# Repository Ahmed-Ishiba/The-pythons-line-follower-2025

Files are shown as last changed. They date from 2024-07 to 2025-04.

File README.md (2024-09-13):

# Robocup-The Pythons

This is a documentation of our journey in the Robocup competition in line-follower category, the team members are Ahmed Ibrahim Elsayed (me), Moaz Ahmed, Eyad Ahmed, Nour Eldin Raoof each are responsible for the programming , electrical and Mechanical part of the robot respectively and our coach Omar Ahmed Khaled.

This documentation will list the components used , the thought process that went into making this robot and the algorithm of our line-following and evacuation zone

## Compontents used:
| Name | Price | Weight | Link|
|---|---|---|-----|
|Pololu wheels|9.95 USD|23gm|https://www.pololu.com/product/3691|
|Omni wheels|35 USD| 49gm|https://www.robotshop.com/products/70mm-omni-wheel-4mm-bore |
|133rpm Motors| 360 EGP|88gm|https://makerselectronics.com/product/dc-motor-with-gear-box-jga25-370-12v-133rpm-20kg-cm |
|Raspberry pi5 8gb ram| 80USD|76gm|https://www.adafruit.com/product/5813|
|Raspberry pi camera module3|35 USD|5gm|https://www.adafruit.com/product/5658|
|Adafruit DRV8871 motor driver|7.5 USD|5gm|https://www.adafruit.com/product/3190|
|Adafruit Time of Flight sensor|14.95 USD|2gm|https://www.adafruit.com/product/3317|
|10 DOF IMU|920 EGP|2gm|https://store.fut-electronics.com/products/10-dof-imu-mpu9250-bmp280?_pos=3&_sid=8a9a77714&_ss=r |
|InfraRed obstacle sensor|75 EGP|3gm|https://store.fut-electronics.com/products/infrared-obstacle-avoidance-sensor-ky-032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|
|Microservo MG90S|140 EGP|17gm|https://makerselectronics.com/product/micro-servo-mg90s-full-metal-gear-180-degree|
|Hiwonder full metal gear|18.99 USD |101gm|https://www.hiwonder.com/products/hps-2018?_pos=16&_sid=3165c6d7c&_ss=r|
|XL 4015 step down dc convertor|115 EGP| 21 gm|https://makerselectronics.com/product/xl4015-step-down-dc-module-with-cv-cc-control|
|LM-2596S DC-DC convertor| 55 EGP |13gm|https://makerselectronics.com/product/lm2596s-dc-dc-converter-3a-step-down-module|
|XL-4016 Step down convertos| 260 EGP|75 gm | https://ampere-electronics.com/product/xl4016-dc-dc-step-down-converter-module-12a-300w/|
|Cytron dual channel motor driver| 1750 EGP | 33gm| https://store.fut-electronics.com/products/dual-channel-dc-motor-driver-10a-each|

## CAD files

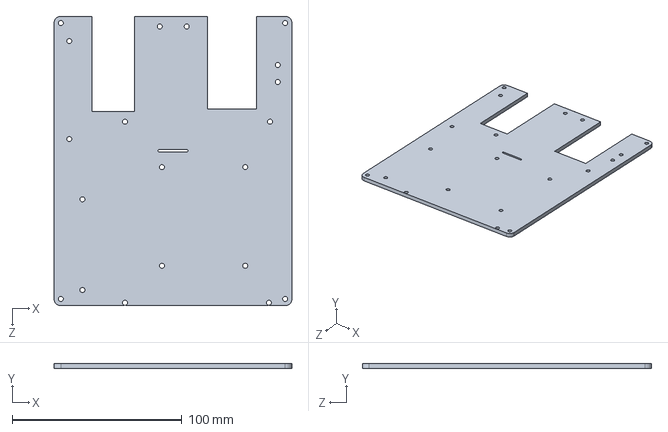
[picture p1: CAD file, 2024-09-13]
mechanical/Floor 2 2nd.SLDPRT
140.0 x 3.00 x 170.3 mm

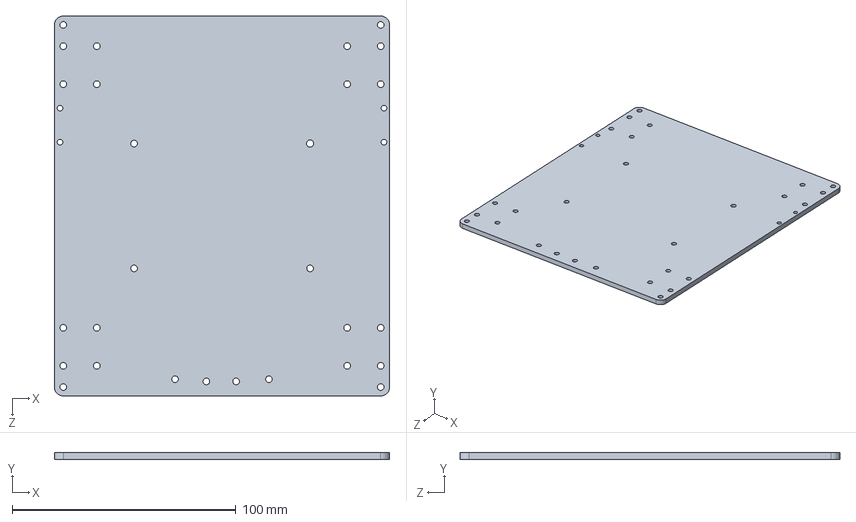
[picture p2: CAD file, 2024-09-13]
mechanical/Floor 1 2nd .SLDPRT
150.0 x 3.00 x 170.0 mm

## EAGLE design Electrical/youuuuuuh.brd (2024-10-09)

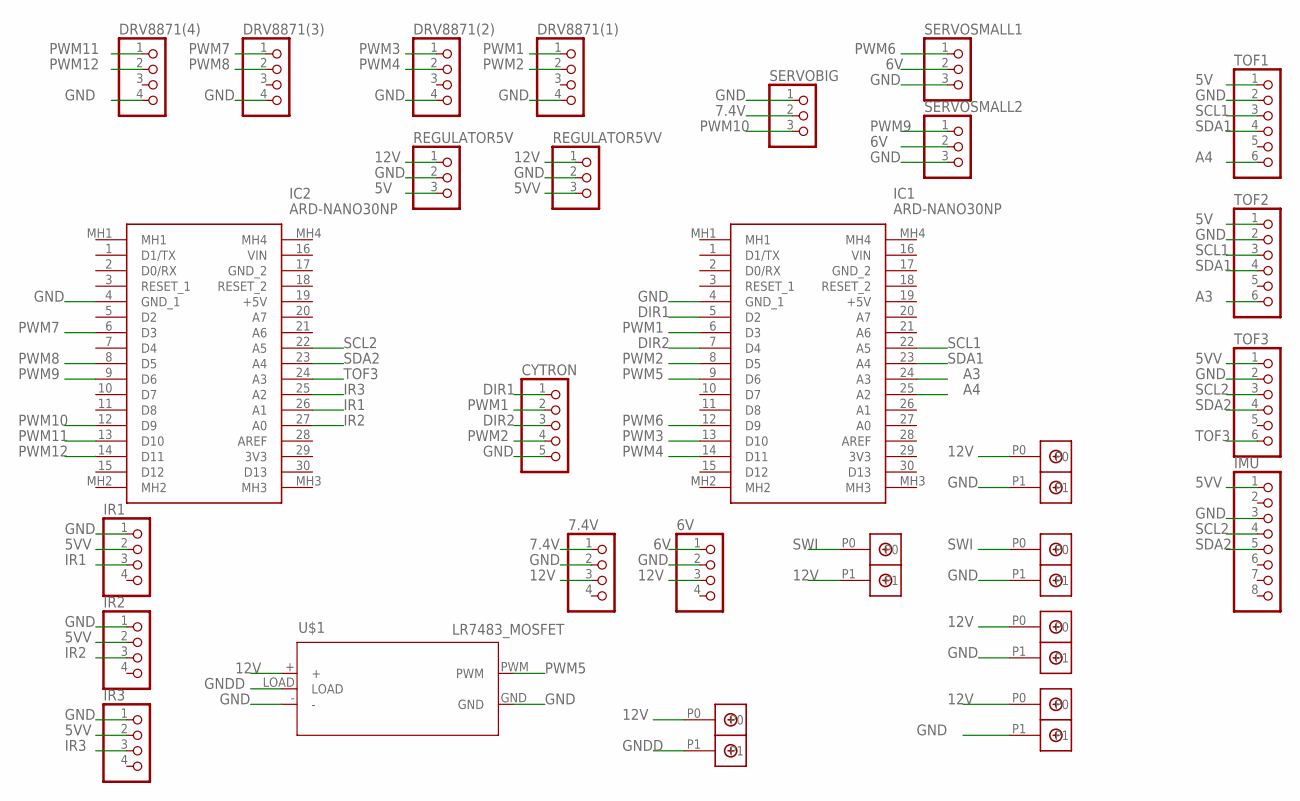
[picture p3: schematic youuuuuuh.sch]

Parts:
6V, 7.4V: PINHD-1X4; 1X04
BATERY: DBCONN-1X2
BUCKSERVO: DBCONN-1X2
CYTRON: PINHD-1X5; 1X05
CYTRONPOWER: DBCONN-1X2
DRV8871(1), DRV8871(2), DRV8871(3), DRV8871(4): PINHD-1X4; 1X04
IC1, IC2: ARD-NANO30NP; ARDNANO30NP
IMU: PINHD-1X8; 1X08
IR1, IR2, IR3: PINHD-1X4; 1X04
LEDS1, LEDS2, LEDS3: DBCONN-1X2
REGULATOR5V, REGULATOR5VV: PINHD-1X3; 1X03
SERVOBIG: PINHD-1X3; 1X03
SERVOSMALL1, SERVOSMALL2: PINHD-1X3; 1X03
TOF1, TOF2, TOF3: PINHD-1X6; 1X06
U$1: LR7483_MOSFET

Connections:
5V: REGULATOR5V.3, TOF1.1, TOF2.1
5VV: IMU.1, IR1.2, IR2.2, IR3.2, REGULATOR5VV.3, TOF3.1
6V: 6V.1, SERVOSMALL1.2, SERVOSMALL2.2
7.4V: 7.4V.1, SERVOBIG.2
12V: 6V.3, 7.4V.3, BUCKSERVO.P0, CYTRONPOWER.P0, LEDS1.P1, LEDS2.P0, LEDS3.P0, REGULATOR5V.1, REGULATOR5VV.1, U$1.+
A3: IC1.24 (A3), TOF2.6
A4: IC1.25 (A2), TOF1.6
DIR1: CYTRON.1, IC1.5 (D2)
DIR2: CYTRON.3, IC1.7 (D4)
GND: 6V.2, 7.4V.2, BATERY.P1, BUCKSERVO.P1, CYTRON.5, CYTRONPOWER.P1, DRV8871(1).4, DRV8871(2).4, DRV8871(3).4, DRV8871(4).4, IC1.4 (GND_1), IC2.4 (GND_1), IMU.3, IR1.1, IR2.1, IR3.1, LEDS2.P1, REGULATOR5V.2, REGULATOR5VV.2, SERVOBIG.1, SERVOSMALL1.3, SERVOSMALL2.3, TOF1.2, TOF2.2, TOF3.2, U$1.-, U$1.GND
GNDD: LEDS3.P1, U$1.LOAD
IR1: IC2.26 (A1), IR1.3
IR2: IC2.27 (A0), IR2.3
IR3: IC2.25 (A2), IR3.3
PWM1: CYTRON.2, DRV8871(1).1, IC1.6 (D3)
PWM2: CYTRON.4, DRV8871(1).2, IC1.8 (D5)
PWM3: DRV8871(2).1, IC1.13 (D10)
PWM4: DRV8871(2).2, IC1.14 (D11)
PWM5: IC1.9 (D6), U$1.PWM
PWM6: IC1.12 (D9), SERVOSMALL1.1
PWM7: DRV8871(3).1, IC2.6 (D3)
PWM8: DRV8871(3).2, IC2.8 (D5)
PWM9: IC2.9 (D6), SERVOSMALL2.1
PWM10: IC2.12 (D9), SERVOBIG.3
PWM11: DRV8871(4).1, IC2.13 (D10)
PWM12: DRV8871(4).2, IC2.14 (D11)
SCL1: IC1.22 (A5), TOF1.3, TOF2.3
SCL2: IC2.22 (A5), IMU.4, TOF3.3
SDA1: IC1.23 (A4), TOF1.4, TOF2.4
SDA2: IC2.23 (A4), IMU.5, TOF3.4
SWI: BATERY.P0, LEDS1.P0
TOF3: IC2.24 (A3), TOF3.6

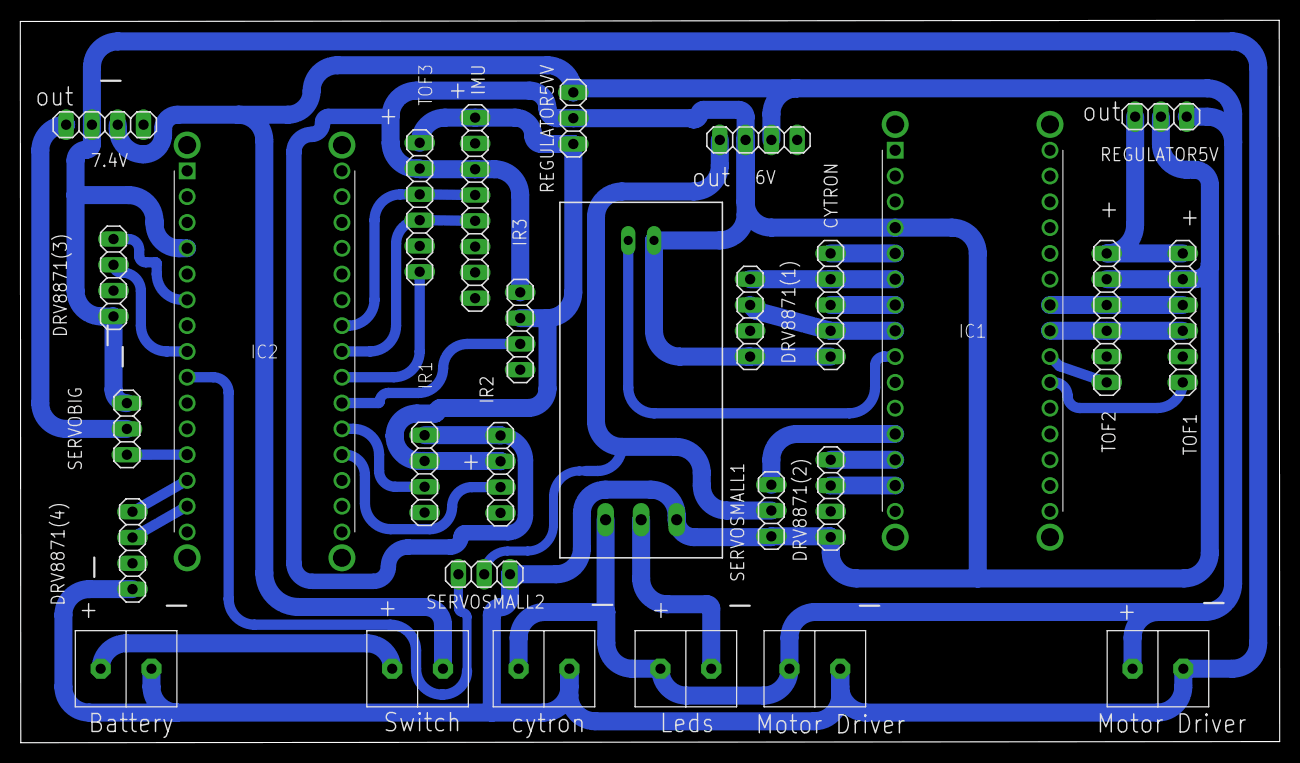
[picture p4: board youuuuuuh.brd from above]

Board: 2 copper layers, 124.0 x 71.1 mm, 28 parts (0 on the bottom side), 32 nets.

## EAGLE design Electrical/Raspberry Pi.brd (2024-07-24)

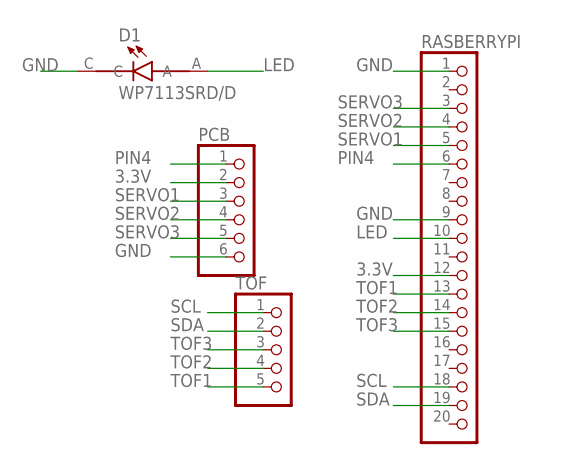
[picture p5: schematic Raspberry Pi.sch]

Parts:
D1: WP7113SRD/D; LED_WP7113SRD/D
PCB: PINHD-1X6; 1X06
RASBERRYPI: PINHD-1X20; 1X20
TOF: PINHD-1X5; 1X05

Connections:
3.3V: PCB.2, RASBERRYPI.12
GND: D1.C, PCB.6, RASBERRYPI.1, RASBERRYPI.9
LED: D1.A, RASBERRYPI.10
PIN4: PCB.1, RASBERRYPI.6
SCL: RASBERRYPI.18, TOF.1
SDA: RASBERRYPI.19, TOF.2
SERVO1: PCB.3, RASBERRYPI.5
SERVO2: PCB.4, RASBERRYPI.4
SERVO3: PCB.5, RASBERRYPI.3
TOF1: RASBERRYPI.13, TOF.5
TOF2: RASBERRYPI.14, TOF.4
TOF3: RASBERRYPI.15, TOF.3

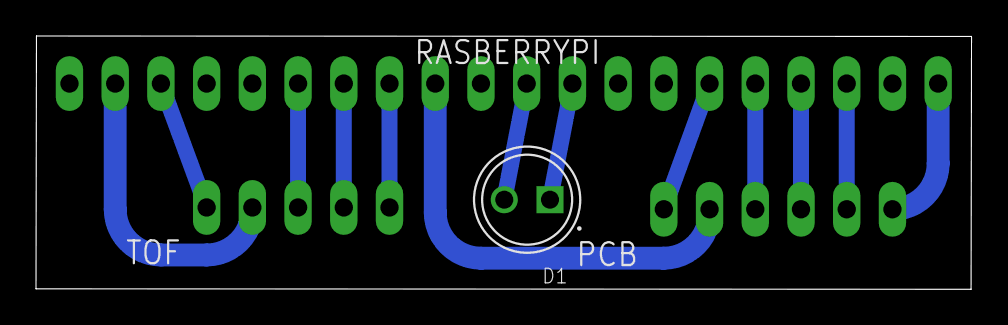
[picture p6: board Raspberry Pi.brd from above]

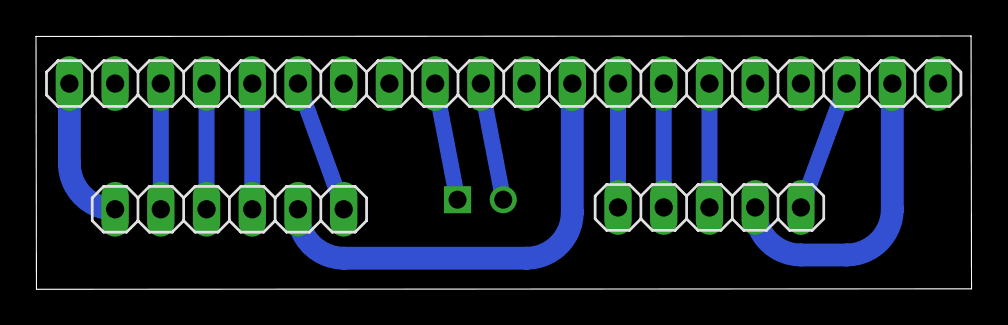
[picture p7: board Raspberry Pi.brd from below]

Board: 2 copper layers, 52.0 x 14.1 mm, 4 parts (3 on the bottom side), 12 nets.

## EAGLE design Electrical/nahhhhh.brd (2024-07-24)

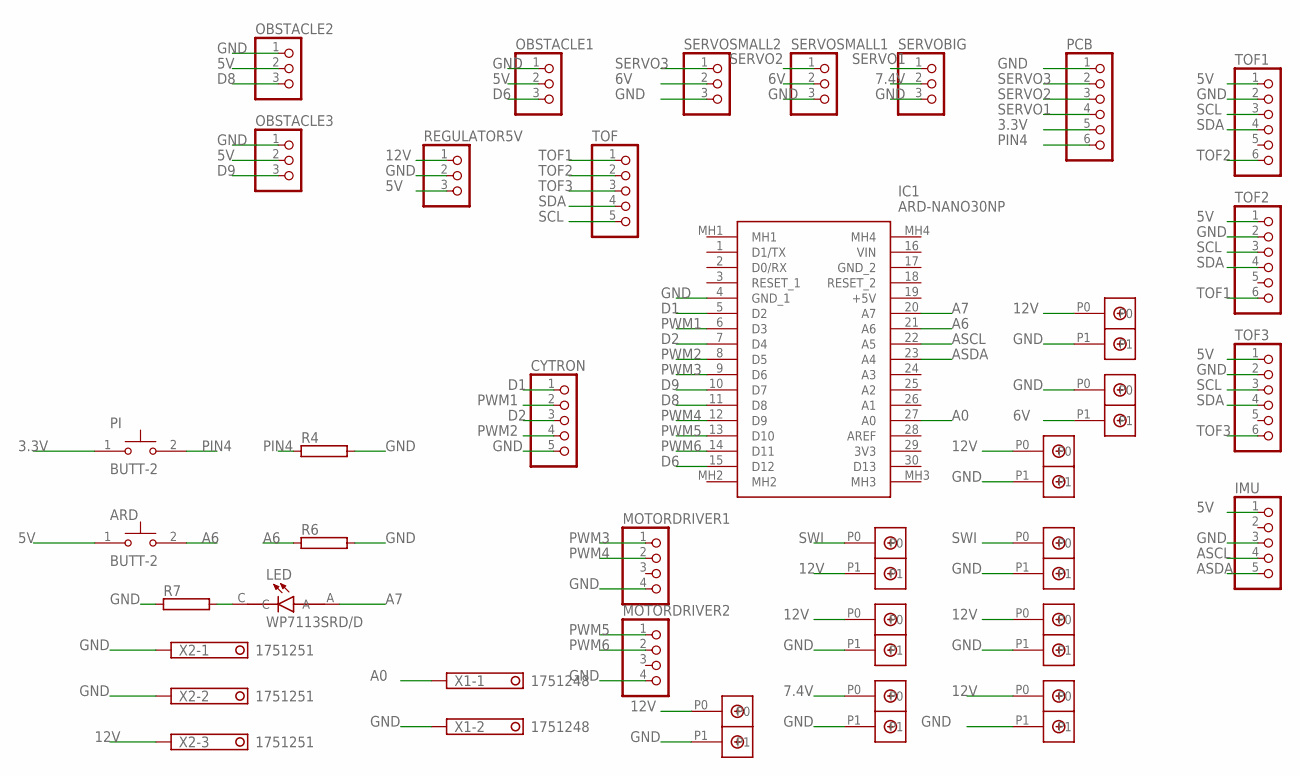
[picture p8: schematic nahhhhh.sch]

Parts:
ARD: BUTT-2; SW_BUTT-2
BATERY: DBCONN-1X2
BUCKSERVO: DBCONN-1X2
CYTRON: PINHD-1X5; 1X05
CYTRONPOWER: DBCONN-1X2
IC1: ARD-NANO30NP; ARDNANO30NP
IMU: PINHD-1X5; 1X05
LED: WP7113SRD/D; LED_WP7113SRD/D
LEDS, LEDS1, LEDS2, LEDS3, LEDS4, LEDS5: DBCONN-1X2
MOTORDRIVER1, MOTORDRIVER2: PINHD-1X4; 1X04
OBSTACLE1, OBSTACLE2, OBSTACLE3: PINHD-1X3; 1X03
PCB: PINHD-1X6; 1X06
PI: BUTT-2; SW_BUTT-2
R4, R6, R7: RHPS58; HPS58
REGULATOR5V: PINHD-1X3; 1X03
SERVOBIG: PINHD-1X3; 1X03
SERVOSMALL1, SERVOSMALL2: PINHD-1X3; 1X03
TOF: PINHD-1X5; 1X05
TOF1, TOF2, TOF3: PINHD-1X6; 1X06
U$1: DBCONN-1X2
X1: 1751248
X2: 1751251

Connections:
3.3V: PCB.5, PI.1
5V: ARD.1, IMU.1, OBSTACLE1.2, OBSTACLE2.2, OBSTACLE3.2, REGULATOR5V.3, TOF1.1, TOF2.1, TOF3.1
6V: LEDS5.P1, SERVOSMALL1.2, SERVOSMALL2.2
7.4V: SERVOBIG.2, U$1.P0
12V: BUCKSERVO.P0, CYTRONPOWER.P0, LEDS.P0, LEDS1.P1, LEDS2.P0, LEDS3.P0, LEDS4.P0, REGULATOR5V.1, X2.3
A0: IC1.27 (A0), X1.1
A6: ARD.2, IC1.21 (A6), R6.1
A7: IC1.20 (A7), LED.A
ASCL: IC1.22 (A5), IMU.4
ASDA: IC1.23 (A4), IMU.5
D1: CYTRON.1, IC1.5 (D2)
D2: CYTRON.3, IC1.7 (D4)
D6: IC1.15 (D12), OBSTACLE1.3
D8: IC1.11 (D8), OBSTACLE2.3
D9: IC1.10 (D7), OBSTACLE3.3
GND: BATERY.P1, BUCKSERVO.P1, CYTRON.5, CYTRONPOWER.P1, IC1.4 (GND_1), IMU.3, LEDS.P1, LEDS2.P1, LEDS3.P1, LEDS4.P1, LEDS5.P0, MOTORDRIVER1.4, MOTORDRIVER2.4, OBSTACLE1.1, OBSTACLE2.1, OBSTACLE3.1, PCB.1, R4.2, R6.2, R7.1, REGULATOR5V.2, SERVOBIG.3, SERVOSMALL1.3, SERVOSMALL2.3, TOF1.2, TOF2.2, TOF3.2, U$1.P1, X1.2, X2.1, X2.2
unnamed: LED.C, R7.2
PIN4: PCB.6, PI.2, R4.1
PWM1: CYTRON.2, IC1.6 (D3)
PWM2: CYTRON.4, IC1.8 (D5)
PWM3: IC1.9 (D6), MOTORDRIVER1.1
PWM4: IC1.12 (D9), MOTORDRIVER1.2
PWM5: IC1.13 (D10), MOTORDRIVER2.1
PWM6: IC1.14 (D11), MOTORDRIVER2.2
SCL: TOF.5, TOF1.3, TOF2.3, TOF3.3
SDA: TOF.4, TOF1.4, TOF2.4, TOF3.4
SERVO1: PCB.4, SERVOBIG.1
SERVO2: PCB.3, SERVOSMALL1.1
SERVO3: PCB.2, SERVOSMALL2.1
SWI: BATERY.P0, LEDS1.P0
TOF1: TOF.1, TOF2.6
TOF2: TOF.2, TOF1.6
TOF3: TOF.3, TOF3.6

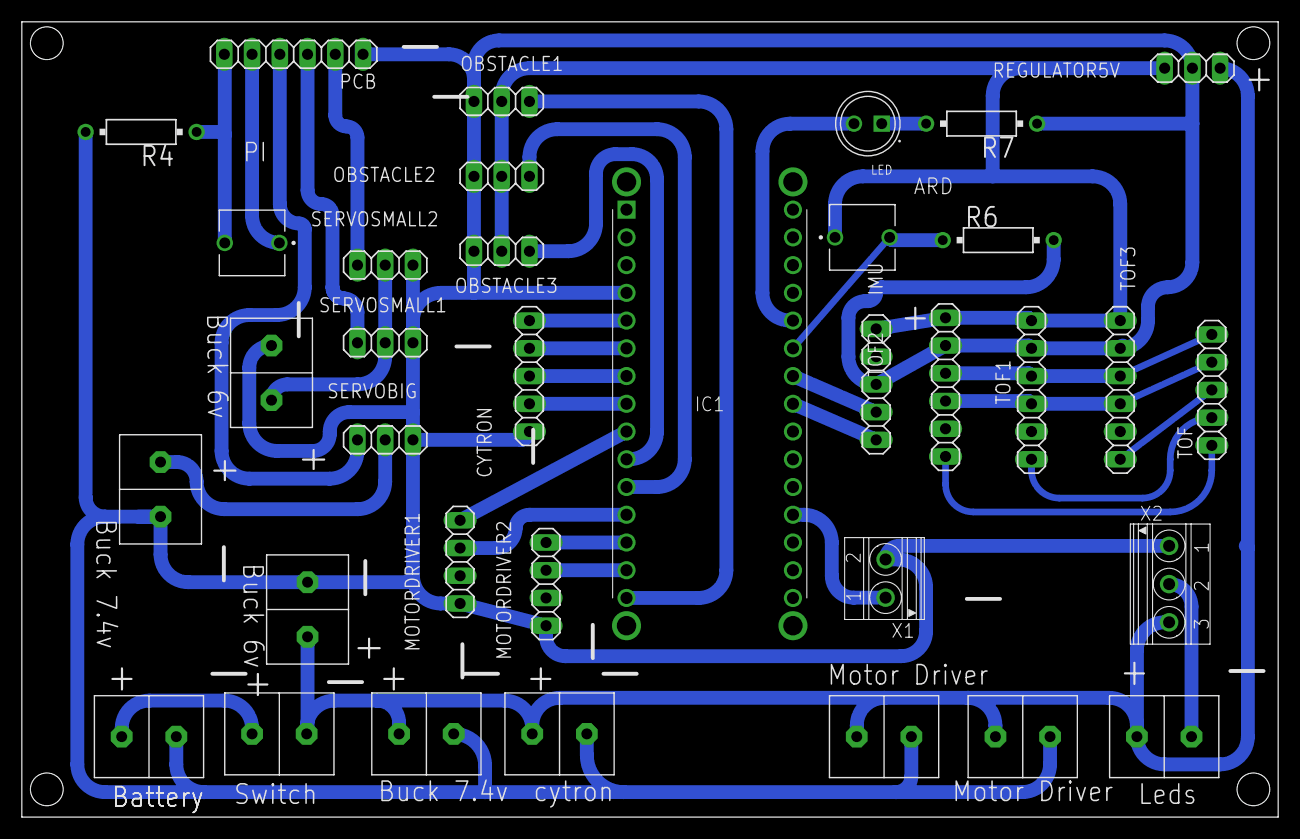
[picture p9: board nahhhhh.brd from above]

Board: 2 copper layers, 115.0 x 72.8 mm, 35 parts (0 on the bottom side), 33 nets.

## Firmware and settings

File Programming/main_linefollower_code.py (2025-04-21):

from __future__ import division

script = True
turn_off_motion = False
turn_off_drawing = True
detect_red = False

import time
from ultralytics import YOLO
import board
import gpiod
import busio
from adafruit_mpu6050 import MPU6050
import Adafruit_PCA9685
import Adafruit_GPIO.I2C as I2C
from adafruit_motor import servo
from adafruit_pca9685 import PCA9685
import os
import sys
import smbus
import cv2
from picamera2 import Picamera2
import numpy as np
import math
from time import sleep
from operator import itemgetter
weights = [0.3,0.6,0.7] 
arr_higher_threshold = [np.array([149,188,176], np.uint8),np.array([149,188,176], np.uint8),np.array([149,188,176], np.uint8)]
arr_lower_threshold = [np.array([115,114,12], np.uint8), np.array([115,114,12], np.uint8), np.array([115,114,12], np.uint8)]

picam2 = Picamera2(0)
picam2.preview_configuration.main.size=(320,240) #full screen : 3280 2464
picam2.preview_configuration.main.format = "RGB888" #8 bits
picam2.start()
centroid_sum = 0
center_pos = 0


i2c = board.I2C()
i2c_bus = 1
pwm = Adafruit_PCA9685.PCA9685(address=0x40, busnum=i2c_bus)
try:
	OFFSET_X = 0
	OFFSET_Y = 0
	OFFSET_Z = 0

	mpu = MPU6050(i2c)
	mpu.accelerometer_offset = (OFFSET_X, OFFSET_Y, OFFSET_Z)
except:
	pass



f = gpiod.LINE_REQ_FLAG_BIAS_PULL_DOWN
chip = gpiod.Chip('gpiochip4')
led = chip.get_line(20)#20
led.request("p_gpio", gpiod.LINE_REQ_DIR_OUT, f)
led.set_value(1)
time.sleep(1)
led.set_value(0)


pca = PCA9685(i2c)
pca.frequency = 50

check_zone = False

pwm.set_pwm_freq(60)

left_front_1 = 14
left_front_2 = 15

left_back_1 = 9
left_back_2 = 8

right_front_1 = 12
right_front_2 = 13

right_back_1 = 10
right_back_2 = 11

high_speed = 900
speed2 =0
low_speed  = 700
zero_speed = 0
counter =0
model = YOLO("/home/pi/yolo/silver_classify_s.onnx", task='classify')
def entrance(im):
    global check_zone
    global counter, enter_zone
    #picam1.set_controls({"AeEnable":False, "ExposureTime":4000}) #To be tested
    results = model.predict(im, imgsz=128, conf=0.2, workers=4,verbose=False)
    result=results[0].numpy()
    confidences = result.probs.top5conf
    silver_value = confidences[0] if result.probs.top1 == 1 else confidences[1]
    print("confidance",silver_value)
    if silver_value >0.2:
        print("saw silver")
        counter+=1
    else:
        counter =0
    if counter > 0:
        enter_zone = True
        print("evacuation")
        """
        with open("/tmp/switch_script","w") as f:
            f.write("switch")
        time.sleep(2)
        """
        
     
    
def calculate_orientation():
    accel_x, accel_y, accel_z = mpu.acceleration
    # Calculate pitch and roll angles
    pitch = math.atan2(accel_x, math.sqrt(accel_y**2 + accel_z**2)) * 180 / math.pi
    roll = math.atan2(-accel_y, accel_z) * 180 / math.pi

    # Convert to range -180 to 180
    if pitch > 180:
        pitch -= 360
    if roll > 180:
        roll -= 360

    return pitch, roll

def map_value(value, from_low, from_high, to_low, to_high):
    if from_high - from_low == 0:
        return to_low  
    mapped_value = (value - from_low) / (from_high - from_low) * (to_high - to_low) + to_low
    return mapped_value

def turn_around():
    backward()
    time.sleep(0.5)
    right(1000)
    time.sleep(1.5)

def forward():
    global speed2
    pwm.set_pwm(left_front_1, 0, 500+speed2)
    pwm.set_pwm(left_front_2, 0, 0)
	
    pwm.set_pwm(left_back_1, 0, 500+speed2)
    pwm.set_pwm(left_back_2, 0, 0)
	
    pwm.set_pwm(right_front_1, 0, 500+speed2)
    pwm.set_pwm(right_front_2, 0, 0)
	
    pwm.set_pwm(right_back_1, 0, 500+speed2)
    pwm.set_pwm(right_back_2, 0, 0)
def backward():
    pwm.set_pwm(left_front_2, 0, 600)
    pwm.set_pwm(left_front_1, 0, 0)
	
    pwm.set_pwm(left_back_2, 0, 600)
    pwm.set_pwm(left_back_1, 0, 0)
	
    pwm.set_pwm(right_front_2, 0, 600)
    pwm.set_pwm(right_front_1, 0, 0)
	
    pwm.set_pwm(right_back_2, 0, 600)
    pwm.set_pwm(right_back_1, 0, 0)
def right(speed):
    pwm.set_pwm(left_front_1, 0, speed)
    pwm.set_pwm(left_front_2, 0, 0)
	
    pwm.set_pwm(left_back_1, 0, 400)
    pwm.set_pwm(left_back_2, 0, 0)
    
    pwm.set_pwm(right_front_2, 0, speed)
    pwm.set_pwm(right_front_1, 0, 0)
	
    pwm.set_pwm(right_back_2, 0, 400)
    pwm.set_pwm(right_back_1, 0, 0)
def left(speed):
    pwm.set_pwm(left_front_2, 0, speed)
    pwm.set_pwm(left_front_1, 0, 0)
	
    pwm.set_pwm(left_back_2, 0, 400)
    pwm.set_pwm(left_back_1, 0, 0)
	
    pwm.set_pwm(right_front_1, 0, speed)
    pwm.set_pwm(right_front_2, 0, 0)
	
    pwm.set_pwm(right_back_1, 0, 400)
    pwm.set_pwm(right_back_2, 0, 0)
def stop():
    pwm.set_pwm(left_front_2, 0, 900)
    pwm.set_pwm(left_front_1, 0, 0)
    pwm.set_pwm(left_back_2, 0, 900)
    pwm.set_pwm(left_back_1, 0, 0)
    pwm.set_pwm(right_front_2, 0, 900)
    pwm.set_pwm(right_front_1, 0, 0)
    pwm.set_pwm(right_back_2, 0, 900)
    pwm.set_pwm(right_back_1, 0, 0)
    time.sleep(0.1)
    pwm.set_pwm(left_front_1, 0, 0)
    pwm.set_pwm(left_front_2, 0, 0)
    pwm.set_pwm(left_back_1, 0, 0)
    pwm.set_pwm(left_back_2, 0, 0)
    pwm.set_pwm(right_front_1, 0, 0)
    pwm.set_pwm(right_front_2, 0, 0)
    pwm.set_pwm(right_back_1, 0, 0)
    pwm.set_pwm(right_back_2, 0, 0)

def obstacle_left():
	left(1000)
	time.sleep(0.6)
	stop()
	time.sleep(0.2)
	forward()
	time.sleep(0.9)
	stop()
	time.sleep(0.2)
	right(1000)
	time.sleep(0.7)
	stop()
	time.sleep(0.2)
	forward()
	time.sleep(1.3)
	stop()
	time.sleep(0.2)
	right(1000)
	time.sleep(0.7)
	stop()
	time.sleep(0.2)
	forward()
	time.sleep(0.7)
	stop()
	time.sleep(0.2)
	left(1000)
	time.sleep(0.7)
	stop()
	time.sleep(5)
	
def obstacle_right():
	right(1000)
	time.sleep(0.6)
	stop()
	time.sleep(0.2)
	forward()
	time.sleep(0.9)
	stop()
	time.sleep(0.2)
	left(1000)
	time.sleep(0.7)
	stop()
	time.sleep(0.2)
	forward()
	time.sleep(1.3)
	stop()
	time.sleep(0.2)
	left(1000)
	time.sleep(0.7)
	stop()
	time.sleep(0.2)
	forward()
	time.sleep(0.7)
	stop()
	time.sleep(0.2)
	right(1000)
	time.sleep(0.7)
	stop()
	time.sleep(5)

"""
hoigher =  (179, 106, 101)
lower =  (91, 27, 12)


"""
black_lower = np.array([91, 27, 12], np.uint8)
black_upper =np.array([179, 106, 101], np.uint8)
def detect_triangles(im):
    cropped_image = im[140:200, 15:305] #140:230,:320
    cx, cy, w, h =0,0,0,0
    triangle_area = 0
    right_zigzag, left_zigzag = False, False
    theta = 0
    global black_lower
    global black_upper
    hsvf = cv2.cvtColor(cropped_image, cv2.COLOR_BGR2HSV)
    black_mask = cv2.inRange(hsvf, black_lower, black_upper)
    black_result = cv2.bitwise_and(cropped_image, cropped_image, mask=black_mask)
    black_contours, black_hierarchy = cv2.findContours(black_mask, cv2.RETR_TREE, cv2.CHAIN_APPROX_SIMPLE)
    if len(black_contours)>0:
        largest_black = max(black_contours, key=cv2.contourArea)
        if not(turn_off_drawing):
            cv2.drawContours(cropped_image,largest_black,-1,(255, 0, 0), 3)
        approx = cv2.approxPolyDP(largest_black, 0.021*cv2.arcLength(largest_black, True), True)#0.025, 0.23
        x, y, w, h = cv2.boundingRect(largest_black)
        print("len approx", len(approx))
        if len(approx) ==3:
            triangle_area = cv2.contourArea(largest_black)
            print("triangle area = ", triangle_area)
            print("approx", approx[0][0][0])
            p1 = (approx[0][0][0], approx[0][0][1])
            p2 = (approx[1][0][0], approx[1][0][1])
            p3 = (approx[2][0][0], approx[2][0][1])
            point_array = [p1, p2, p3]
            point_array = sorted(point_array, key = itemgetter(1))
            print(point_array)
            a = point_array[0]
            b = point_array[1] #down left point
            c = point_array[2] #down right point
            
            distance_ab = math.dist(a, b)
            distance_ac = math.dist(a, c)
            
            vector_AB = (b[0]-a[0], b[1]-a[1])
            vector_AC = (c[0]-a[0], c[1]-a[1])
            dot_AB_AC = vector_AB[0]*vector_AC[0] + vector_AB[1]*vector_AC[1]
            theta = math.acos((dot_AB_AC)/(distance_ab*distance_ac))
            cv2.circle(cropped_image, a, 5, (255, 255, 255), 3)
            cv2.circle(cropped_image, b, 5, (0, 0, 255), 3)
            cv2.circle(cropped_image, c, 5, (255, 0, 0), 3)
            
            if theta <5 and triangle_area > 50 :
                
                if distance_ab > distance_ac:    # >
                    triangle_x = b[0]
                    print("left zigzag test")
                    left_zigzag = True
                    '''
                    if triangle_x >160:
                        #print("right zigzag")
                        right_zigzag = True
                    elif triangle_x < 160:
                        #print("left zigzag")
                        left_zigzag = True
                    '''
                elif distance_ac> distance_ab: #>
                    triangle_x = c[0]
                    print("right zigzag test")
                    right_zigzag = True
                    '''
                    if triangle_x >160:
                        right_zigzag = True
                        #print("right zigzag")
                    elif triangle_x < 160:
                        left_zigzag = True
                        #print("left zigzag")
                    '''
                print("distance of AB", distance_ab)
                print("distance of AC", distance_ac)
                #if not(turn_off_drawing):
                cv2.drawContours(cropped_image,largest_black,0,(255, 255, 0), 3)
    
            else:
                left_zigzag = False
                right_zigzag = False
        else:
            left_zigzag = False
            right_zigzag = False
        #cx = int(x) + int(w/2)
        #cy = int(y) + int(h/2)
    return right_zigzag, left_zigzag, theta, triangle_area

"""
hoigher =  (175, 80, 92)
lower =  (3, 0, 29)
""" 
right_array = []
left_array = []
is_black =0
omar_right_counter =0 
omar_left_counter =0
readings_range=75
def omar_function(live):
    cropped_image = [live[140:200, 15:55],live[140:200,265:305]] 
    cx, y, w, h =0,0,0,0
    global right_array
    global omar_right_counter
    global omar_left_counter 
    global left_array 
    global is_black
    global black_lower
    global black_upper
    for i,region in enumerate(cropped_image):
        
        hsvf = cv2.cvtColor(region, cv2.COLOR_BGR2HSV)
        black_mask = cv2.inRange(hsvf, black_lower, black_upper)
        black_result = cv2.bitwise_and(region, region, mask=black_mask)
        black_contours, black_hierarchy = cv2.findContours(black_mask, cv2.RETR_TREE, cv2.CHAIN_APPROX_SIMPLE)
        is_black =0
        if black_contours:
            largest_black = max(black_contours, key=cv2.contourArea)
            area = cv2.contourArea(largest_black)
            x, y, w, h = cv2.boundingRect(largest_black)
            
            if area >150:
                cv2.rectangle(region,(x,y),(x+w,y+h), (255,0,0), 2)
                is_black = 1
        if i == 1:
            if len(right_array)==readings_range:
                omar_right_counter += -1 if right_array[0] else 1
                del right_array[0]
            right_array.append(is_black)
            omar_right_counter +=1 if is_black else -1
        elif i == 0:
            if len(left_array)==readings_range:
                omar_left_counter += -1 if left_array[0] else 1
                del left_array[0]
            left_array.append(is_black)
            omar_left_counter += 1 if is_black else -1
            
    omar_left_counter = readings_range if omar_left_counter >readings_range else omar_left_counter
    omar_left_counter = -readings_range if omar_left_counter <-readings_range else omar_left_counter
    
    omar_right_counter = readings_range if omar_right_counter >readings_range else omar_right_counter
    omar_right_counter = -readings_range if omar_right_counter <-readings_range else omar_right_counter
        
    

def black(live):
    #cropped_image = [live[70:110,15:305],live[120:160,15:305],live[170:240, 15:305]] #y, x
    #cropped_image = [live[90:130,15:305],live[140:180,15:305],live[190:240, 15:305]] #y, x
    cropped_image = [live[80:110,15:305],live[120:160,15:305],live[170:200, 15:305]] #y, x
    global detect_black #cropped_image = [live[90:130,15:305],live[140:180,15:305],live[190:240, 15:305]] y, x
    #cropped_image = [live[80:120,15:305],live[130:170,15:305],live[180:230, 15:305]] #y, x 2adema sh8al kelaby
    centroid_sum = 0 
    cy = 0
    cx_array =[]
    cy_correction_array = [80, 120, 170]
    cy_array = []
    area_array = []
    black_contour_list = []
    deflection_angle = 0
    w = 0
    center_pos = 0
    main_x =0
    cx = 0
    h = 0
    last_width = 0
    last_area = 0
    info_tuple = []
    area = 0
    gap_counter =0
    weight_sum=0
    
    for i,region in enumerate(cropped_image):
        cx_diff = 160
        last_cy = 0
        global black_lower
        global black_upper
        hsvf = cv2.cvtColor(region, cv2.COLOR_BGR2HSV)
        black_mask = cv2.inRange(hsvf, black_lower, black_upper)
        black_result = cv2.bitwise_and(region, region, mask=black_mask)
        black_contours, black_hierarchy = cv2.findContours(black_mask, cv2.RETR_TREE, cv2.CHAIN_APPROX_SIMPLE)
        if len(black_contours) > 0:
            largest_black = max(black_contours, key=cv2.contourArea)
            selected_black=largest_black
            area = cv2.contourArea(selected_black)
            if(area > 800):
       
                print("area",area)
                #cv2.drawContours(region, largest_black, -1, (255, 0, 0), 3)
                #print("x of black line", x)
                print("height of black",h)
                #return cx, cy
                black_contours = sorted(black_contours, key = cv2.contourArea, reverse=True)
                for blacks in black_contours:
                    area = cv2.contourArea(blacks)
                    if area < 800:
                        break
                    M = cv2.moments(blacks)
                    if M["m00"] != 0:
                        cx =int(M["m10"]/M["m00"])
                        cy =int(M["m01"]/M["m00"]) + cy_correction_array[i]
                        
                    if i ==2:
                        print("cx ", cx)
                        print("cy ", cy)
                        
                        print("last cy ", last_cy)
                        print("cx diffrence ", cx_diff)
                        
                        if cy > last_cy and abs(cx-160) <cx_diff:
                            selected_black = blacks
                            last_cy = cy
                            
                            cx_diff=abs(cx-160)
                            print("last cy", last_cy)
                        x, y, w, h = cv2.boundingRect(selected_black)
                        main_x = x
                        last_width = w
                    else:
                        if abs(cx-160) <cx_diff:
                            selected_black = blacks
                            cx_diff=abs(cx-160)
                area = cv2.contourArea(selected_black)
                M = cv2.moments(selected_black)
                if M["m00"] != 0:
                    cx =int(M["m10"]/M["m00"])
                    cy =int(M["m01"]/M["m00"]) + cy_correction_array[i]
                    
                    if len(cx_array) and i==1 and abs(cx-cx_array[0])>100:
                        cx_array[0]=0
                    cx_array.append(cx)
                    info_tuple.append((cx,cy, area))
                    cv2.circle(region, (cx, cy- cy_correction_array[i]), 2, (255, 0, 0), 1)
                x, y, w, h = cv2.boundingRect(selected_black)
                #cv2.rectangle(region,(x,y),(x+w,y+h), (220,220,220), 2)
            else:
                cx_array.append(0)
        else:
            cx_array.append(0)
    detect_black =False
    for reg in cx_array:
        if reg:
            detect_black = True
            break
    if detect_black:
        for f in range(0,len(cx_array)):
            #print("cx array", cx_array[f])
            centroid_sum += cx_array[f] * weights[f] # r[4] is the roi weight.
            weight_sum += weights[f]*bool(cx_array[f])
        center_pos = (centroid_sum / weight_sum)
        print("center position = ", center_pos)
        deflection = (center_pos-145)/(100)
        deflection_angle = math.degrees(math.atan(deflection))
            
    return cx, cy, last_area, last_width, h, deflection_angle, gap_counter, center_pos, info_tuple, main_x
"""
hoigher =  (10, 203, 255)
lower =  (0, 89, 174)


"""

def red(im):
    cropped_red_image = im[90:240, :] #y, x
    green_blobs = []
    global detect_red
    cx = 0
    cy = 0
    w = 0
    h = 0
    area = 0
    red_lower = np.array([0, 89, 174], np.uint8)
    red_upper = np.array([10, 203, 255], np.uint8)
    hsvf_red = cv2.cvtColor(cropped_red_image, cv2.COLOR_BGR2HSV)
    red_mask = cv2.inRange(hsvf_red, red_lower, red_upper)
    red_result = cv2.bitwise_and(cropped_red_image, cropped_red_image, mask=red_mask)
    red_contours, red_hierarchy = cv2.findContours(red_mask, cv2.RETR_TREE, cv2.CHAIN_APPROX_SIMPLE)
    red_contours=sorted(red_contours,key=cv2.contourArea, reverse=True)
    if len(red_contours) >0:
        largest_red = max(red_contours, key=cv2.contourArea)
        area = cv2.contourArea(largest_red)
        print("area:",area)
        if area >1150:
            detect_red = True



"""
hoigher =  (88, 187, 178)
lower =  (59, 109, 122)
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

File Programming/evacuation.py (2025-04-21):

from __future__ import division
from ultralytics import YOLO
import cv2
from picamera2 import Picamera2
import serial
from time import sleep
import numpy as np
import board
import gpiod
import busio
import Adafruit_PCA9685
import Adafruit_GPIO.I2C as I2C
from adafruit_motor import servo
from adafruit_pca9685 import PCA9685
from libcamera import Transform
chip = gpiod.Chip('gpiochip4')
line = chip.get_line(7)#20
f = gpiod.LINE_REQ_FLAG_BIAS_PULL_DOWN
line.request("p_gpio", gpiod.LINE_REQ_DIR_IN, f)
i2c = board.I2C()
i2c_bus = 1
pwm = Adafruit_PCA9685.PCA9685(address=0x40, busnum=i2c_bus)

pca = PCA9685(i2c)
pca.frequency = 50

define = False

pwm.set_pwm_freq(60)

left_forward_1 = 14
left_forward_2 = 15

left_back_1 = 9
left_back_2 = 8

right_forward_1 = 12
right_forward_2 = 13

right_back_1 = 10
right_back_2 = 11

high_speed = 700
turn_speed = 600
low_speed  = 525
zero_speed = 0
def forward():
    pwm.set_pwm(left_forward_1, 0, high_speed)
    pwm.set_pwm(left_forward_2, 0, zero_speed)
    pwm.set_pwm(left_back_1, 0, high_speed)
    pwm.set_pwm(left_back_2, 0, zero_speed)
    pwm.set_pwm(right_forward_1, 0, high_speed)
    pwm.set_pwm(right_forward_2, 0, zero_speed)
    pwm.set_pwm(right_back_1, 0, high_speed)
    pwm.set_pwm(right_back_2, 0, zero_speed)
def backward():
    pwm.set_pwm(left_forward_2, 0, high_speed)
    pwm.set_pwm(left_forward_1, 0, zero_speed)
    pwm.set_pwm(left_back_2, 0, high_speed)
    pwm.set_pwm(left_back_1, 0, zero_speed)
    pwm.set_pwm(right_forward_2, 0, high_speed)
    pwm.set_pwm(right_forward_1, 0, zero_speed)
    pwm.set_pwm(right_back_2, 0, high_speed)
    pwm.set_pwm(right_back_1, 0, zero_speed)
def right():
    pwm.set_pwm(left_forward_1, 0, turn_speed)
    pwm.set_pwm(left_forward_2, 0, zero_speed)
    pwm.set_pwm(left_back_1, 0, low_speed)
    pwm.set_pwm(left_back_2, 0, zero_speed)
    pwm.set_pwm(right_forward_2, 0, turn_speed)
    pwm.set_pwm(right_forward_1, 0, zero_speed)
    pwm.set_pwm(right_back_2, 0, low_speed)
    pwm.set_pwm(right_back_1, 0, zero_speed)
def right_narrow():
    pwm.set_pwm(left_forward_1, 0, high_speed)
    pwm.set_pwm(left_forward_2, 0, zero_speed)
    pwm.set_pwm(left_back_1, 0, high_speed)
    pwm.set_pwm(left_back_2, 0, zero_speed)
    pwm.set_pwm(right_forward_2, 0, high_speed)
    pwm.set_pwm(right_forward_1, 0, zero_speed)
    pwm.set_pwm(right_back_2, 0, high_speed)
    pwm.set_pwm(right_back_1, 0, zero_speed)
def right_semi():
    pwm.set_pwm(left_forward_1, 0, turn_speed)
    pwm.set_pwm(left_forward_2, 0, zero_speed)
    pwm.set_pwm(left_back_1, 0, low_speed)
    pwm.set_pwm(left_back_2, 0, zero_speed)
    pwm.set_pwm(right_forward_2, 0, zero_speed)
    pwm.set_pwm(right_forward_1, 0, zero_speed)
    pwm.set_pwm(right_back_2, 0, zero_speed)
    pwm.set_pwm(right_back_1, 0, zero_speed)
def left():
    pwm.set_pwm(left_forward_2, 0, turn_speed)
    pwm.set_pwm(left_forward_1, 0, zero_speed)
    pwm.set_pwm(left_back_2, 0, low_speed)
    pwm.set_pwm(left_back_1, 0, zero_speed)
    pwm.set_pwm(right_forward_1, 0, turn_speed)
    pwm.set_pwm(right_forward_2, 0, zero_speed)
    pwm.set_pwm(right_back_1, 0, low_speed)
    pwm.set_pwm(right_back_2, 0, zero_speed)
def left_semi():
    pwm.set_pwm(left_forward_2, 0, zero_speed)
    pwm.set_pwm(left_forward_1, 0, zero_speed)
    pwm.set_pwm(left_back_2, 0, zero_speed)
    pwm.set_pwm(left_back_1, 0, zero_speed)
    pwm.set_pwm(right_forward_1, 0, turn_speed)
    pwm.set_pwm(right_forward_2, 0, zero_speed)
    pwm.set_pwm(right_back_1, 0, low_speed)
    pwm.set_pwm(right_back_2, 0, zero_speed)
def stop():
    pwm.set_pwm(left_forward_2, 0, high_speed)
    pwm.set_pwm(left_forward_1, 0, zero_speed)
    pwm.set_pwm(left_back_2, 0, high_speed)
    pwm.set_pwm(left_back_1, 0, zero_speed)
    pwm.set_pwm(right_forward_2, 0, high_speed)
    pwm.set_pwm(right_forward_1, 0, zero_speed)
    pwm.set_pwm(right_back_2, 0, high_speed)
    pwm.set_pwm(right_back_1, 0, zero_speed)
    sleep(0.1)
    pwm.set_pwm(left_forward_1, 0, zero_speed)
    pwm.set_pwm(left_forward_2, 0, zero_speed)
    pwm.set_pwm(left_back_1, 0, zero_speed)
    pwm.set_pwm(left_back_2, 0, zero_speed)
    pwm.set_pwm(right_forward_1, 0, zero_speed)
    pwm.set_pwm(right_forward_2, 0, zero_speed)
    pwm.set_pwm(right_back_1, 0, zero_speed)
    pwm.set_pwm(right_back_2, 0, zero_speed)

small_servo = servo.Servo(pca.channels[1], min_pulse=600, max_pulse=2900)
big_servo = servo.Servo(pca.channels[4],  min_pulse=500, max_pulse=2600, actuation_range=270)
door_servo = servo.Servo(pca.channels[7], min_pulse=600, max_pulse=2900)

big_servo.angle = 230
small_servo.angle = 40
door_servo.angle = 10
sleep(0.5)

model = YOLO('best_n.pt')#ball_detect_s.pt
picam2 = Picamera2(1)
picam2.vflip = True  # Flip vertically
picam2.hflip = True  # Flip horizontally
picam2.preview_configuration.main.size=(320,240) #full screen : 3280 2464
picam2.preview_configuration.main.format = "RGB888" #8 bits
picam2.start()

silver_ball = 0
black_ball = 0
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
